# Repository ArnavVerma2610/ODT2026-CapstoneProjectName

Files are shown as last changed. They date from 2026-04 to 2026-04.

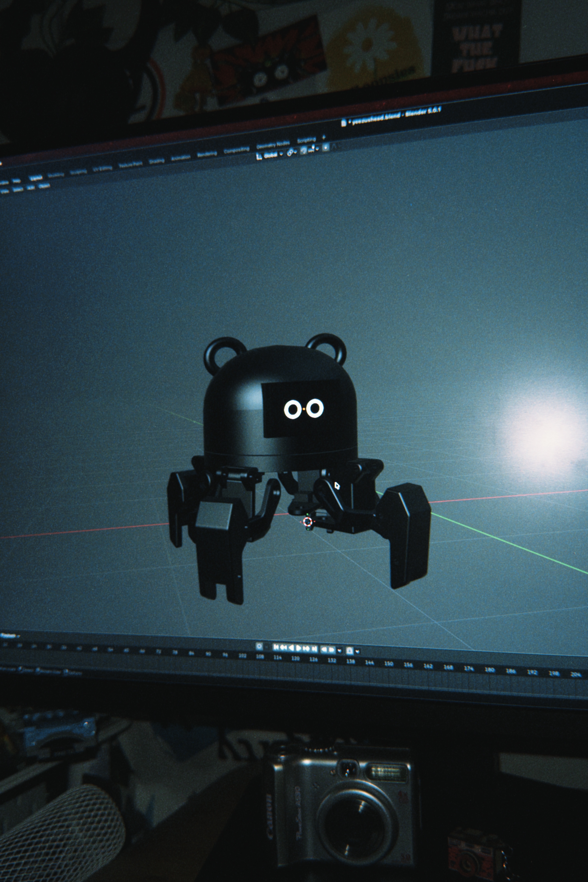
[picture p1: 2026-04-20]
Mechanical Details/Media/3D Visualization.JPG

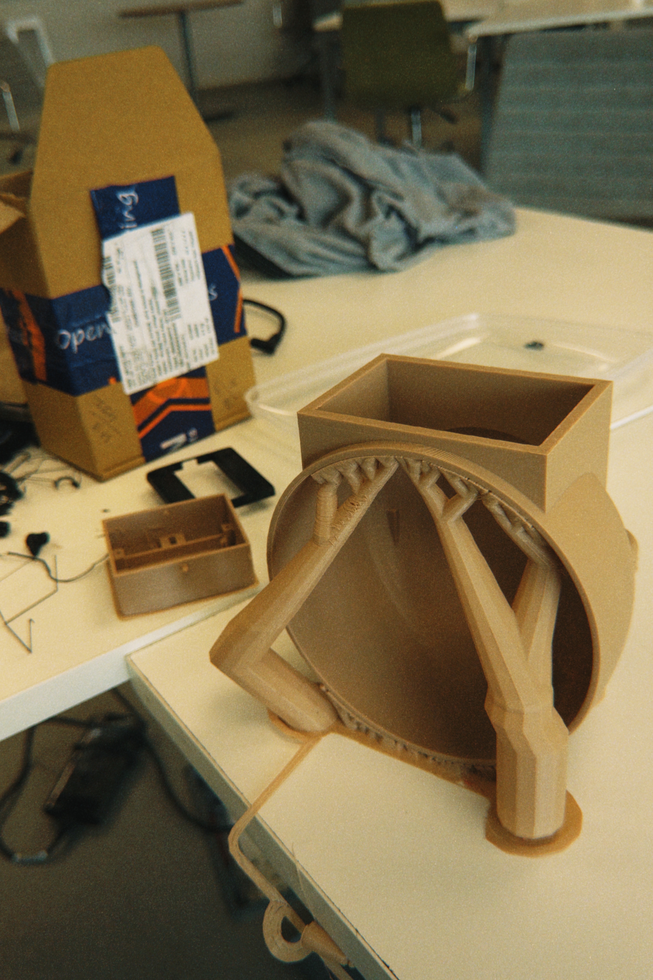
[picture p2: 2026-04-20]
Mechanical Details/Media/Head Print.JPG

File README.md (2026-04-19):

**Project Title**

Yeezus

**📌 Project Overview**

We are creating a small and friendly robot pet for entertainment purposes. It dances, greets, and even plays songs! Carrying with it a visualizer screen for both songs and character animations, it has 4 legs and can execute complex movements.

**📂 Repository Structure**
1. Electronics Details
2. Mechanical Details
3. Software Details
4. Project Documents
5. Media

**⚙️ How to Navigate This Repository**

Electronics Details → Circuit, components justification

Mechanical Details → Sketches, CAD, and fabrication

Software Details → Code, logic, and implementation

Project Documents → Design thinking, planning, testing

Media → Weekly progress and final output

**👥 Team Members**
Arnav Verma
Swayam Tayalia

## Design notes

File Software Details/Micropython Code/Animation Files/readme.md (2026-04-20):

Contains the original image sequence aswell as the .bin file flashed onto the ESP32

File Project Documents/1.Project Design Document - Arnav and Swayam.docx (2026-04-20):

# Project Design Document

### 1. Design Intent

- We set out to create a very fun and lighthearted experience with this project, create a fun project with ourselves to test our limits as people who had never touched electronics before this module began, to being a cute pet for people to look at and get attached to.
- It’s meant to act almost like a first prototype for a robotic pet for a kid, complete with animations and music aiming to stimulate.

### 2. Inspiration & References

- Inspired by Rocky from Project Hail Mary, R2D2 from Star Wars, The Graduation Bear by Kanye West

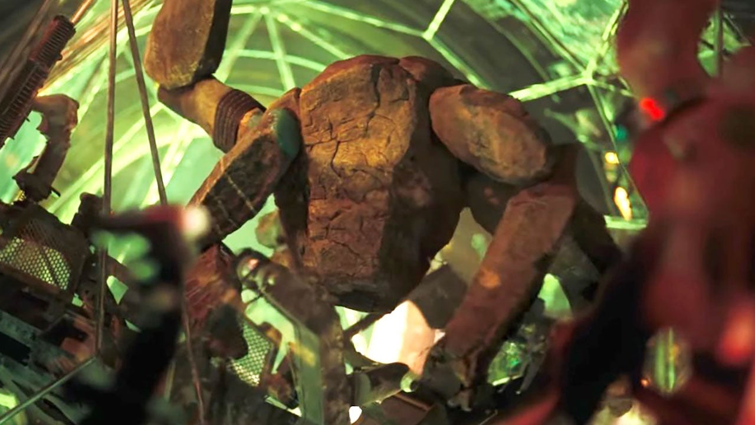
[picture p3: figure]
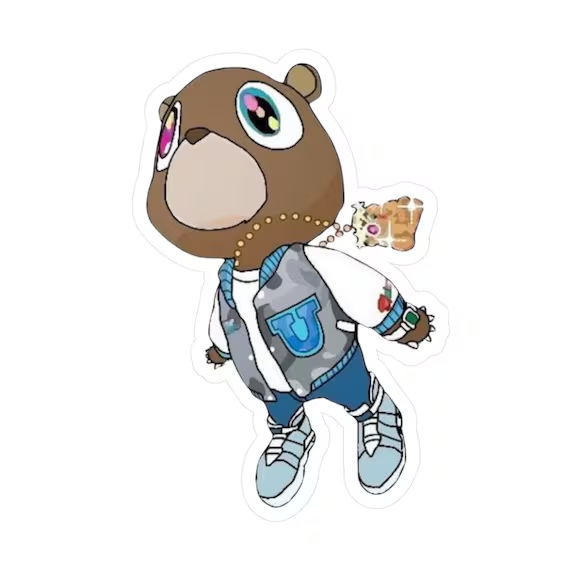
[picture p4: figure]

### 3. User Journey

Step-by-step experience of the user:

1. A user walks by this robot, standing on its stage, with a tablet beside it explaining what it is, what is does.
2. Intrigued, the user decides to flip the switch behind the bot’s head.
3. Suddenly, it comes to life, with a fun robotic voice and an animation making it seem friendly, it introduces itself, YeezyBot.
4. It goes through it’s routine, dances to a song, idles to a Mario Theme, and finally, it walks towards you, wanting to be your friend :)

### 4. Success Criteria

Define measurable success:

- Speaker and Animations startup in <1 second of each other
- User experience relies on the user only turning a switch on, and not having to interfere with any of the servo positions
- Animation goes through the entire 2:35 minute routine uninterrupted
- The robot doesn’t tip over or walk off its stage

### 5. System Overview

Yeezybot is an ESP32-based quadruped that performs a walking/dance routine with on-board OLED animation and audio playback. The ESP32 runs MicroPython and drives three peripheral subsystems . An I2C link (SCL=22, SDA=21, 400 kHz) talks to a PCA9685 16-channel PWM controller, which generates 50 Hz servo pulses for the eight leg servos — four hip joints and four knee joints arranged as a diagonal-trot gait with rear-biased back-lean to compensate for the front-heavy chassis. A dedicated SPI bus (SCK=18, MOSI=23, DC=2, RST=4, CS=5, 20 MHz) streams a 1,210-frame MONO_VLSB animation ( comp4.bin ) to a 128×64 SSD1309 OLED, with frame advances interleaved into the servo step loop so playback never stalls the walk. A DFPlayer Mini, driven over UART with its serial command protocol, plays the matching audio track from microSD in lockstep with the dance routine.

### 6. High-Level Block Diagram

👉 Visual diagram of system components and flow

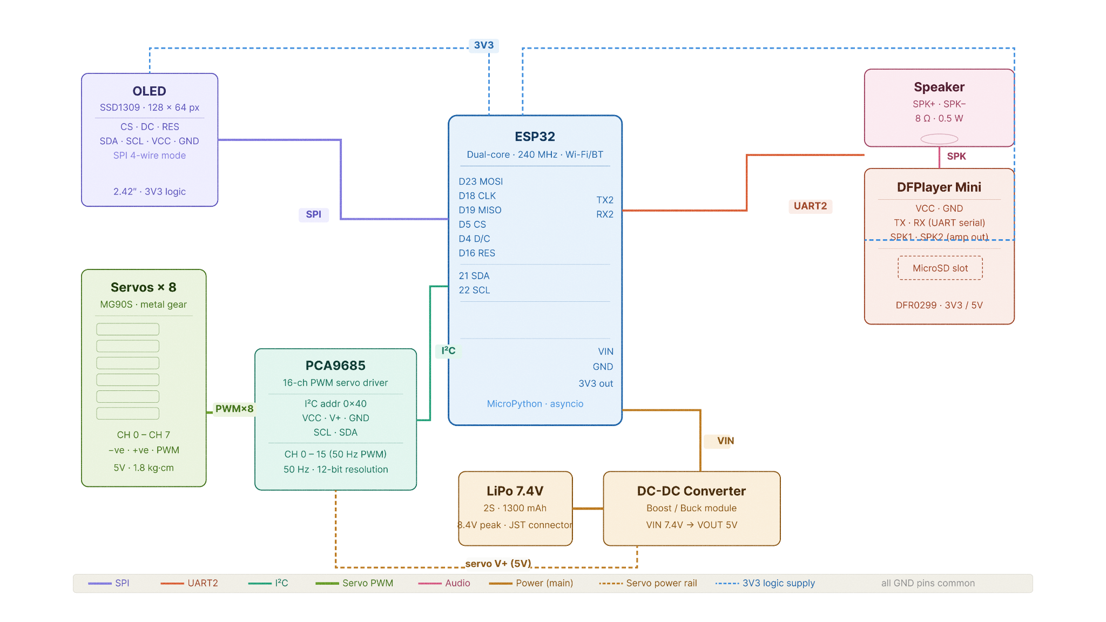
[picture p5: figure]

### 7. Input / Output Mapping

Input | Process | Output
7.4V power supply | Buck convertor | 5v power
Servo channels to pca9685 channels | Servo driver/i2c | Individual control over servos
esp32 | Pca9685 through SCL AND SDA | Control over channels on the driver
Micro SD Card | DF Player Mini | .mp3 files played over speaker
Imag sequences as bin files | SPI | OLED Display

### 8. Sketches & Concepts

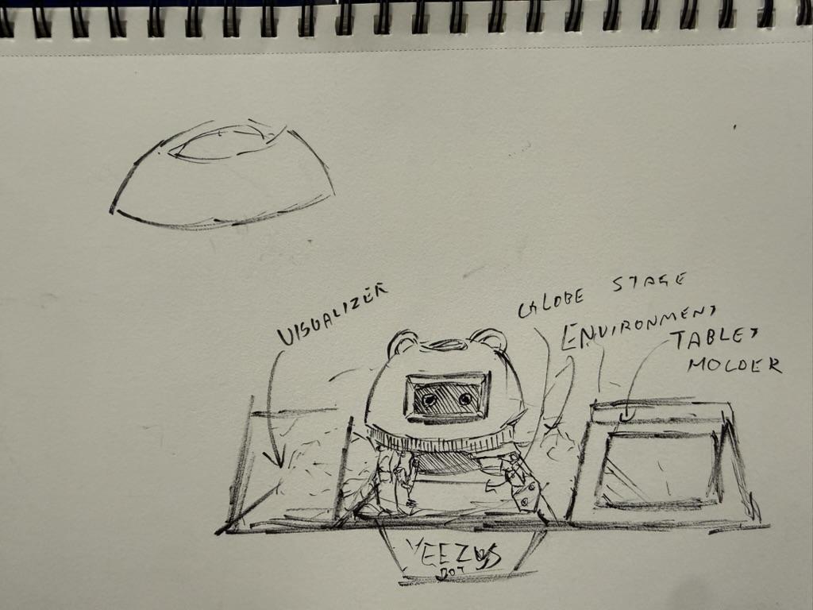
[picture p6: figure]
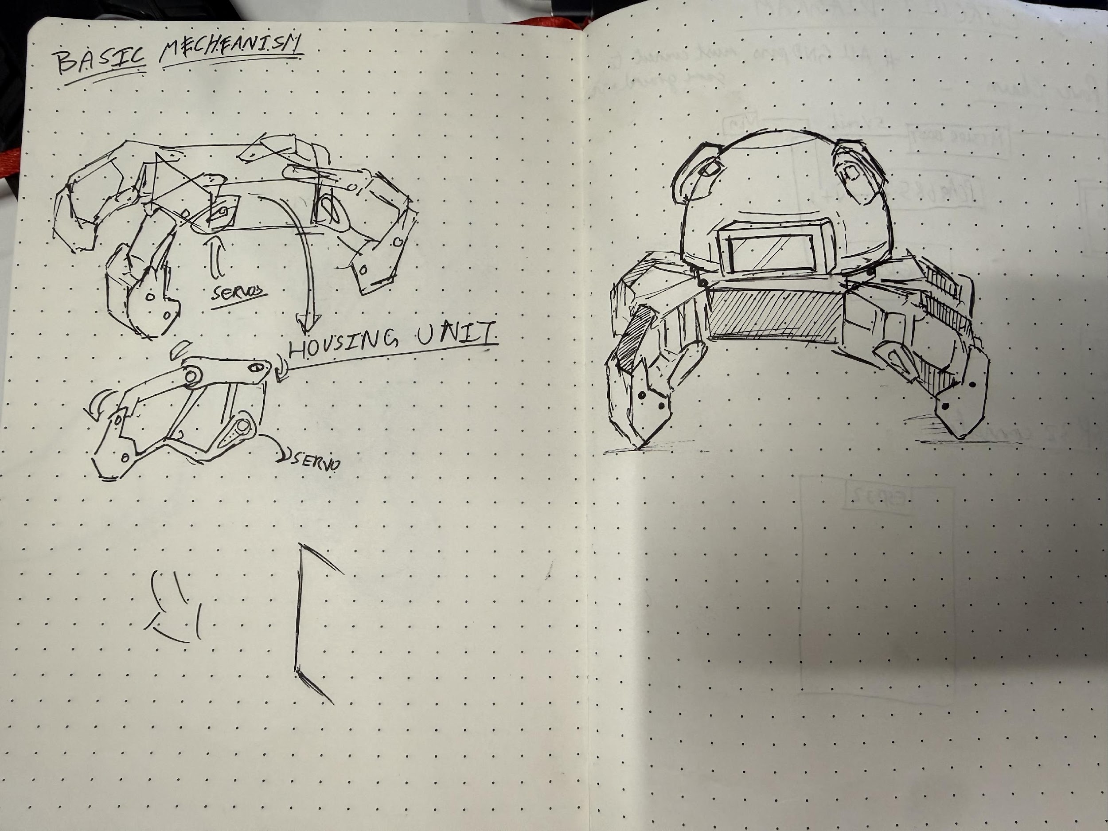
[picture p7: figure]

### 9. Final System Architecture (Labelled)

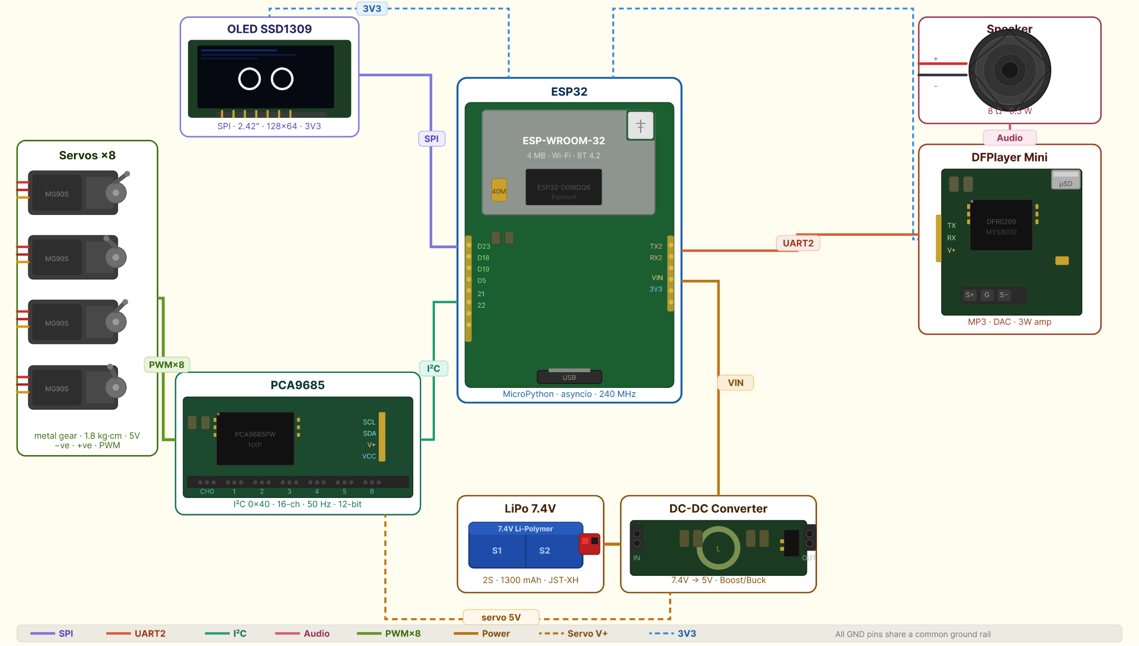
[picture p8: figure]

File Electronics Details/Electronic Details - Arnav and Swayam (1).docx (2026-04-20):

# Electronics Documentation

### 1. Electronics Block Diagram

INITIAL BLOCK DIAGRAM:

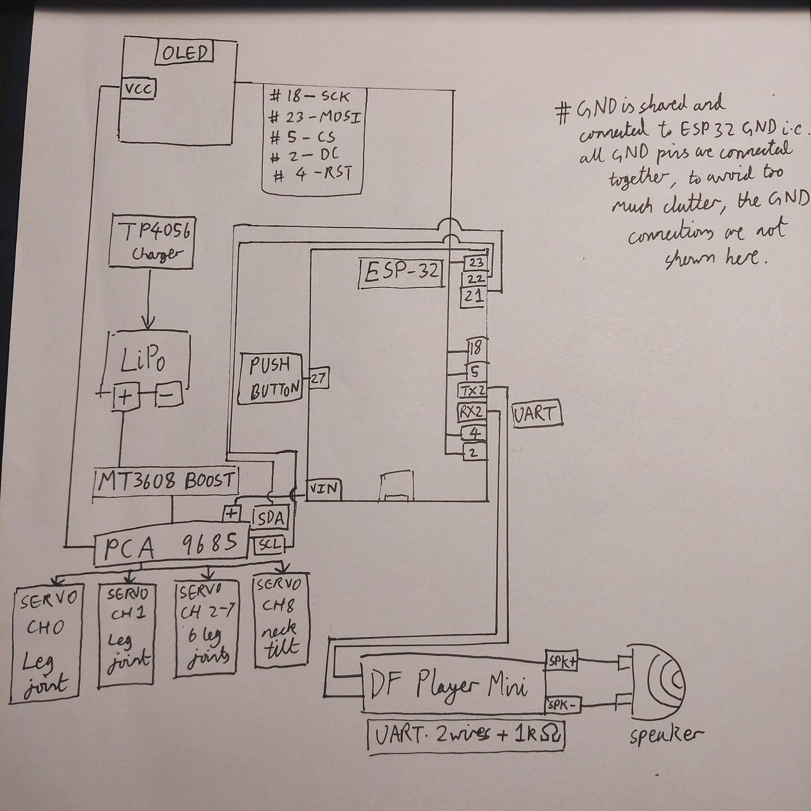
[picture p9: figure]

FINAL CIRCUIT/BLOCK DIAGRAM: (without updated switch connections)

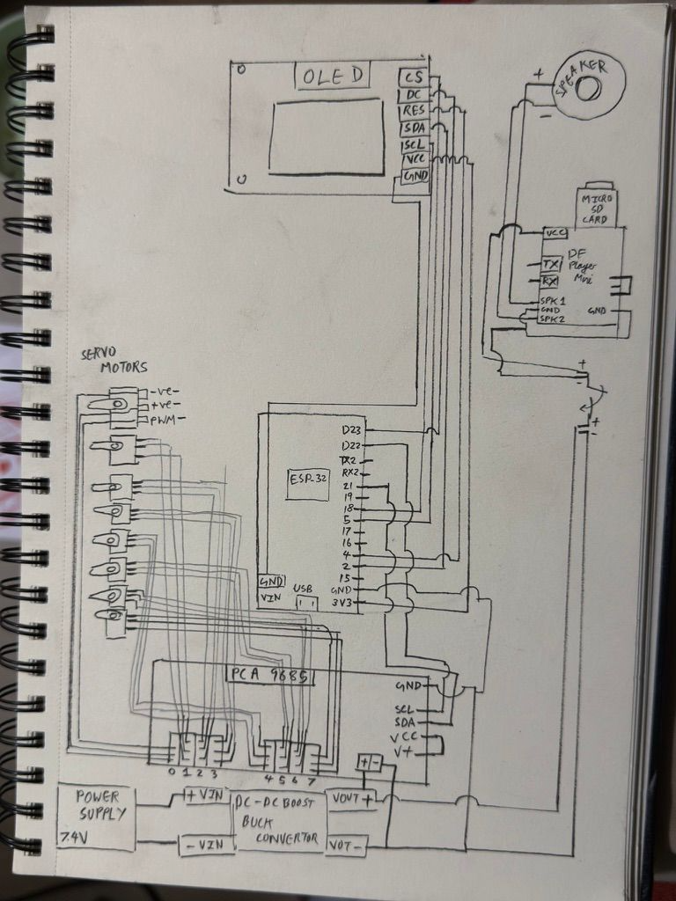
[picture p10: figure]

### 2. Components Table

Component | Quantity | Purpose | Justification
MG90 Servo motors | 8 | To move the individual hip and knee for all four legs in the quadropod | Servos provide robust and smooth motion and are small enough and multiple can be controlled at a time
PCA9685 | 1 | Provides PWM signals to control the position of multiple servo motors using i2c | We need a driver for all the servos and this is the most reliable one
DC-DC BOOST BUCK CONVERTOR | 1 | Converts incoming 7.4v to 5v | We need constant 5v power supply to the electronics in this circuit. We checked this using a multimeter
DF PLAYER MINI | 1 | Used to playback mp3 music from an sd card | Low cost mp3 module designed for audio playback and doesnt need to be connected to a microcontroller to just normally play audio tracks,avoids complexity
Speaker | 1 | Speaker is used to output the audio from the df player | We chose a 8 ohm, 0.5W cause of its small form factor and ease
ssd1309 oled display | 1 | Takes bit map images sent to it and converts it into sequences displayed on the screen | We chose this 2.4 inch display due to it’s high quality oled and larger pixel grid size

Justification is important

DETAILED OVERVIEW OF SERVO MOTORS AND CALIBRATION ‘

Each servo was connected to the channels of the pca9685 i.e. channels 1 to 7.

After this, each servo was placed into the 3d printed units, which would later prove to be a mistake as we had not calibrated it properly yet.

I originally tried to use the concept of oscillator, i.e. the sin wave concept inspired by how keyframe animations in the free software bottango.

We tried doing that in bottango:

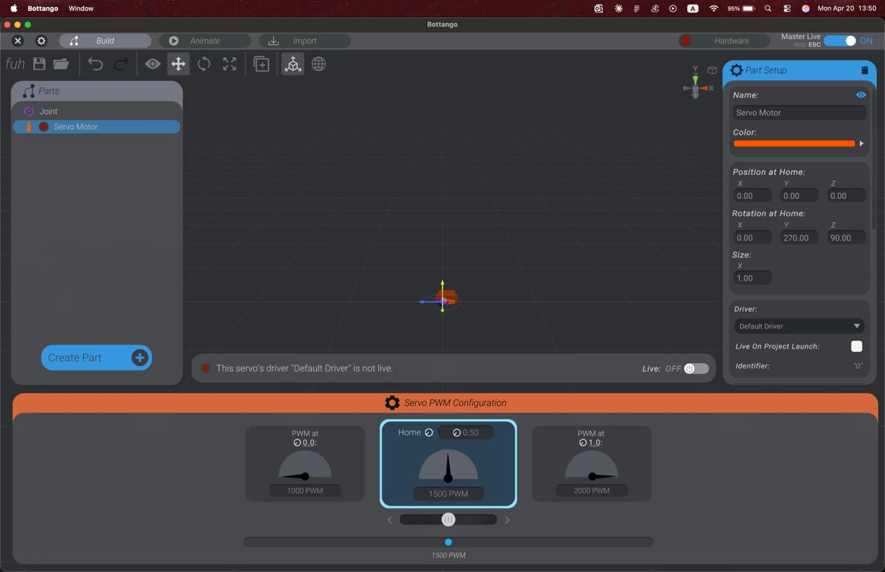
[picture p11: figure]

However, it failed as we were unable to convert the code into the numbers required for the servo animation and we struggled to understand what to extract from the C++ code.

We then decided we have to manually calibrate each servo

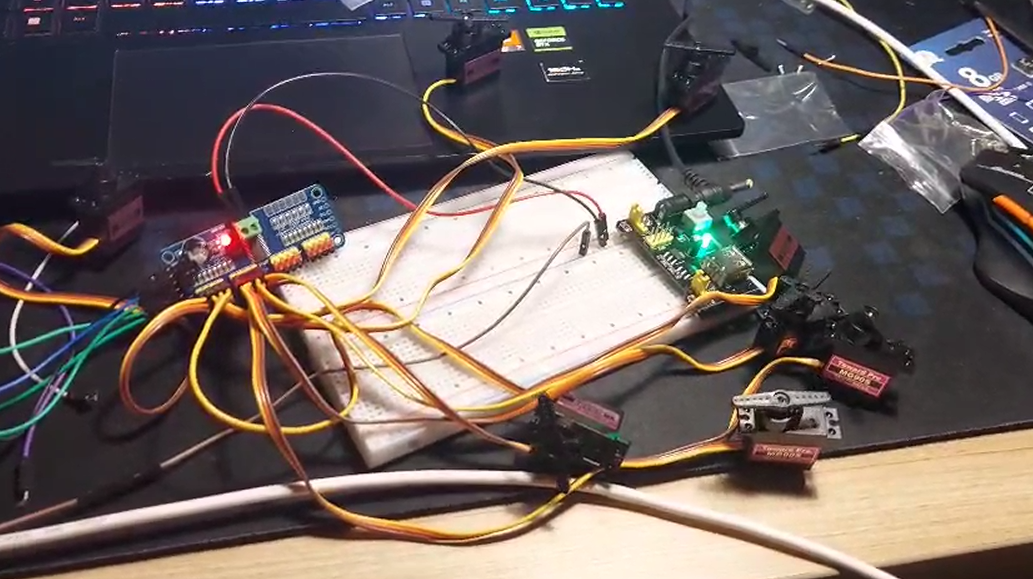
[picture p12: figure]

FOR THE CALIBRATION:

We ran an i2c based library for the pca9685. We then used it to run the respective servo movements for each channel and tested the direction of rotation and the angle swept, after heaps of trial and error not only with the direction of movement but making sure the shaft does not lock out of the housing of the hip and knee indentations cause calibration gets faulty once that happened.

We finally decided on the final calibration for each servo:

# Ch 0 = Front-Right TOP (hip) home=0 moves 0→90 (0=standing)

# Ch 1 = Front-Left TOP (hip) home=90 moves 90→0 (90=standing)

# Ch 2 = Back-Left TOP (hip) home=0 moves 0→90 (0=standing)

# Ch 3 = Back-Right TOP (hip) home=90 moves 90→0 (90=standing)

# Ch 4 = Front-Right BOTTOM (knee) home=0 moves 0→150 (0=standing)

# Ch 5 = Front-Left BOTTOM (knee) home=150 moves 150→0 (150=standing)

# Ch 6 = Back-Left BOTTOM (knee) home=0 moves 0→150 (0=standing)

# Ch 7 = Back-Right BOTTOM (knee) home=130 moves 130→0 (130=standing)

OLED LIBRARY AND CONNECTIONS WE USED FOR THE OLED:

BIN SEQUENCES FIRST DISPLAYED ON OLED USING TERMINAL

THE DF PLAYER MINI WAS WIRED DIRECTLY TO THE POWER SUPPLY AND SPEAKER AND MICRO SD CARD WAS USED TO STORE .MP3 FILES WHICH WERE PLAYED SEQUENTIALLY.

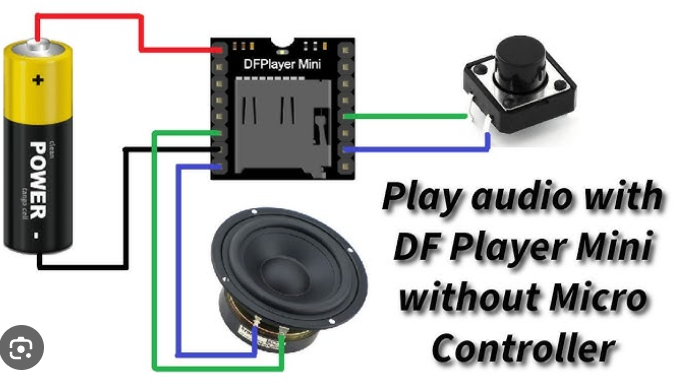
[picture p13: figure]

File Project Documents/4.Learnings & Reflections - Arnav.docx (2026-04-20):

# Learnings & Reflections Document

### 1. Team Reflection

The team worked to their strengths, each worked on different aspects of design, code, and hardware depending on what their strong suits were.

The ease of communication and work ethic helped ease workflow.

Team dynamics in terms of planning and overall execution of final result could be improved,

### 2. Technical Reflection

(add OLED and image bitmap related technical challenges here)

Key technical challenges:

DEBUGGING/PITFALLS FACED:

- MAKING THE INITIAL BLOCK DIAGRAM WAS TRICKY AND NOT THE MOST RELIABLE
- WOKWI SIMULATIONS FAILED TO WORK
- MODIFYING AND DESIGNING OUR PARTS IN FUSION TO FACILITATE SMOOTH MOVEMENTS TO FIT EACH MG90 WAS TEDIOUS
- BOTTANGO SIMS FAILURE
- SERVO CALIBRATION ISSUES
- OSSCILATOR ANIMATION SEQUENCE VERY UNRELIABLE, HARD-CODED ANGLE MOVEMENTS PREFERRED INSTEAD
- OLED INTERFACING, SPI CONNECTION FOR SSD1309 WAS MORE DIFFICULT THAN IF IT WAS I2C
- TRANSFERRING BITMAP IMAGE SEQUENCES TO THE OLED PROVED DIFFICULT IN MICROPYTHON COMPARED TO TERMINAL.
- GETTING THE OLED TO WORK ALONG WITH THE SERVOS INVOLVED

LEARNINGS:

SOFTWARE:

In terms of software, we learned a lot about how different protocols work, such as 12c, SPI, UART and how they depend on the data-driven and the supply of power they draw from. We also learned a lot about how to make sure to use external drivers to move servos, i.e., assigning channels to them, calling the functions to adjust the angles, and determining mean positions through trial and error.

We also learned about how OLEDs work and how they convert images into bitmaps, and how SPI connections work, along with the correct prompt engineering to correctly convert the image sequences and display them through the terminal and later Python.

We learnt how to use oscillator math functions such as sin(2pi + phase offset) , which didn't end up working, but also made us more confident in hard function calling and angle resent animation based solely on the list of angles between max and min after calibration.

We got through code flashing and created an MIT App Inventor base app to run different animated commands, such as walk, dance

HARDWARE:

Getting all the parts 3d printed and then getting all the parts sanded, taking off supports was harder than expected cause we had to also model a lot of the mg90 attachment parts inside of fusion while taking reference from repos online such as https://github.com/dorianborian/sesame-robot/

Figuring out the m3 scews and hard clamp fits while not already calibrating the servos was very difficult and then having to calculate the angles which trying and failing at an oscillation sine curve type movement was a waste of time

End of the day calibrating and setting max and min values to each servo and carefully placing them in the housing was the main part

On the final day , assembling all the parts was causing weight issues as the physics of the weight of all components and the battery proved to heavily hamper the final output

### 3. Design Reflection

From a design point of view our end result matched the initial ideation stages pretty well, the look of the robot was pretty similar to out initial sketches.

The experience far surpassed our intentions.

- The experience of it definitely matched the intent we originally we went out with. We thought this would be a much simpler robot, maybe move left or right a little, but not really do much, definitely not a fully choreographed dance sequence and be able to walk around, but that’s the fun part of ambition, that even after all of that, we’re still left with a semi-satisfied feeling. That’s important though, that’s the only feeling that will really drive us forward and push us to improve for the next time we dabble in this field.

### 4. Personal Reflection

What did I end up learning throughout this module? Everything. Despite my preconceived notions of not having loved Computer Science too much during my high school years, I ended up loving the process of interfacing physical electronics with code in this module and realized that perhaps that tactility was the missing link in me developing a love for this field. I truly enjoyed my time throughout the module and only wished we’d gone through this sooner. I really struggled with the hardware part since code was just a more familiar and comfortable medium for me but slowly throughout the module I understood what worked and it all started clicking for me. I even started a few side projects of my own and dug deeper into this rabbit hole, even though it’s actively burning a hole in my pocket. Thank you to Nayan for really guiding me throughout this, couldn’t have made it through without you.

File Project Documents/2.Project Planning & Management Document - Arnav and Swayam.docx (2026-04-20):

# Project Planning & Management Document

### 1. Project Overview

- Name: YeezyBot
- Team: Arnav Verma and Swayam Tayalia
- Overview: We are creating a small and friendly robot pet for entertainment purposes. It dances, greets, and even plays songs! Carrying with it a visualizer screen for both songs and character animations, it has 4 legs and can execute complex movements.

### 2. Team Roles & Responsibilities

Member Name | Role | Responsibilities
Arnav Verma | Software and Creative Elements | OLED Animation, Servo Animation, 3D Modeling, Media, Documentation, Video Editing, Diorama Creation, MIT App, and HTML File
Swayam Tayalia | Hardware Wiring and Software Testing | Housing unit and legs assembly, Servo Wiring, Servo Calibration and Troubleshooting, Speaker Electronics, 3D Modeling, Diorama Creation, Documentation

👉 Clearly define who is responsible for what (software, electronics, documentation, etc.)

### 3. Project Timeline & Milestones

Week | Goals | Deliverables | Status
Week 0 | Iterate over what the design should be , its functionality, feasibility and basic circuitry | Project design , idea and function | complete
Week 1 | Get 3d files ready and component list,block diagram | 3d print files, components order | complete
Week 2 | 3d parts ready to assemble and | 3d printed parts , components connected and tested | complete
Week 3 | Final project ready with at least 2 animation cycles | Final hardware assembly and complete software integration | Tentative - janky setup

👉 Break project into weekly achievable goals

### 4. Weekly Progress Log

A table for each week:

Week 0

- Planned Tasks: think and iterate over a project idea
- Completed Tasks: finalised an idea
- Challenges Faced: going from extremely complex idea to a slightly less complex one
- Solutions: focus on step by step process and not go in head first
- Next Steps: gather parts, circuit diagram , plan out the next weeks

Week 1

- Planned Tasks: get a complete circuit diagram, order the parts, get reference from other github repositories online as well as quadropod videos on youtube.

Get the 3d print files ready, edit and modify existing files as well as put new files

- Completed Tasks: got a complete block diagram and ordered parts
- Challenges Faced: tried and failed simulating in wokwi
- Solutions: ask nayan
- Next Steps: refine the idea, wait for parts and start assembling,testing

Week 2

- Planned Tasks: test and start putting components and circuits together, get parts 3d printed
- Completed Tasks: tested components, failed to simulate in wokwi completely, few failed prints , but rest of the prints worked.
- Challenges Faced: having to change the circuit diagram and having to refer to many repos online and yt vids to figure the correct connections
- Solutions: do more research and work fast
- Next Steps: do final circuit, test out animations, prepare final code and assembly

Week 3

- Planned Tasks: do final circuit, test out animations, prepare final code and assembly
- Completed Tasks: final circuit, animations - janky , final code
- Challenges Faced: weight distribution , connection issues, hefty components to fit inside small space., janky animations
- Solutions: improve connections, modify entire project to counteract the weight of the battery and other components
- Next Steps: work on new animation cycles, better walk and dance and do more research to see how project can be modified to balance weight better.

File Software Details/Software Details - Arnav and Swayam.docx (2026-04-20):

# Software Documentation

### 1. Software Overview

SOFTWARE COMPONENTS:

OLED BITMAP IMAGE SEQUENCES

SERVO MOTOR LISTS AND FUNCTIONS FOR THEIR MOVEMENT

DIFFERENT CYCLES FOR THE SERVO MOTOR including WALK and DANCE Cycles.

PLATFORMS USED:

Micropython, Bottango, Terminal (for the test of the OLED Display)

The software handles the primary code, importing libraries from machine including i2c,spi and uart protocol logic.

The primary code contains the oled library import with the bin images and the servo controls.

### 2. System Logic

1.User turns on the switch or plugs in the micro-USB

2. The power supplies 7.4V to a buck converter

3. The DC-DC boost buck convertor steps down the voltage to 5V

4. The signal goes to the DF Player mini to access the files from the micro-SD card that end with .mp3 and plates them sequentially through the connected speaker.

5. The OLED Starts displaying the bitmap image sequences from a preset animation that was created and then converted to this format to be displayed on to the screen

6. The HOME POSITION of the servos gets triggered i.e. the mean position of the servos.

7. The Burst animation is triggered

8. DANCE - animation cycle is triggered - twist, lean , tilt , wave etc.

9. The USB is connected and a walking cycle animation can be played using walk cycle code on laptop that can be adjusted per cycle.

10. Animation ends, music stops , returns back to HOME position.

3.FLOWCHART:

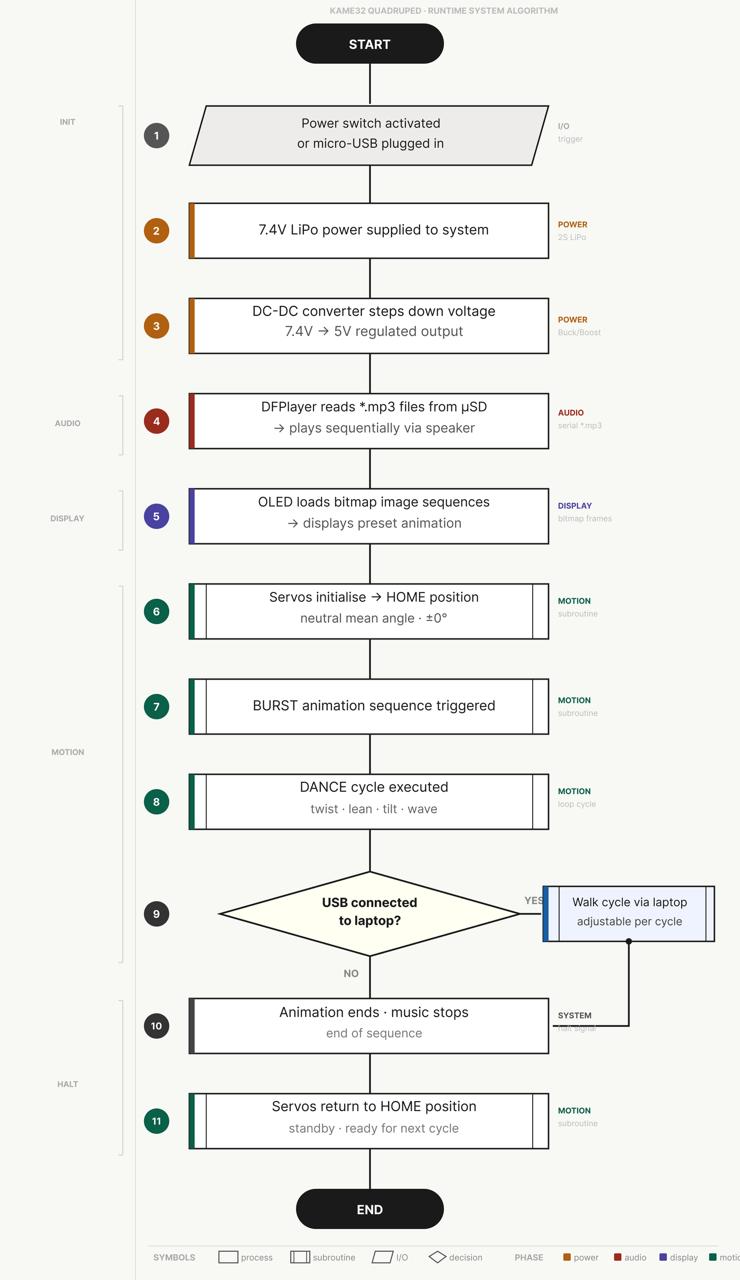
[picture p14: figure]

### 4. App Flow (If MIT App Inventor)

Base MIT App Inventor (Used as a stepping stone to the HTML Website)

- Start Scanning → scans for BLE devices, populates list live
- ListView tap → selects device
- Connect → connects to selected device
- Disconnect → disconnects
- CobraKai / Bob / Wave / Dance → all four send identical byte [1] to the ESP32 (bug — never differentiated, meant to be fixed in html file)
- Clock timer polls for incoming strings, displays them in status label

HTML File

- Start Scanning → opens browser's native BLE picker
- Device tap → selects device
- Connect / Disconnect → same behavior
- CobraKai / Dance / Wave / Bob → each sends a function call

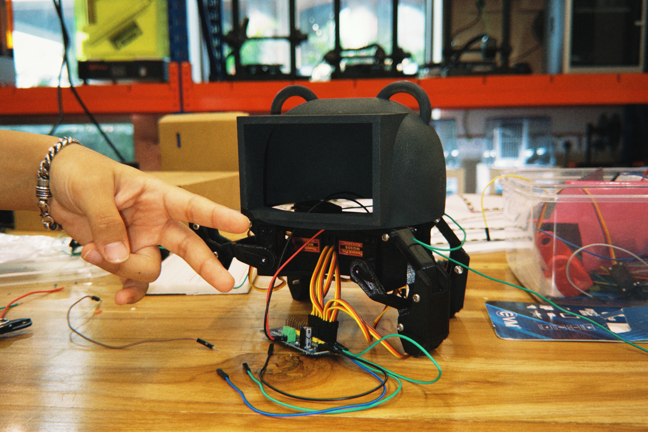
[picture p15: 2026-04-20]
Mechanical Details/Media/Head ontop of Body Frame.JPG

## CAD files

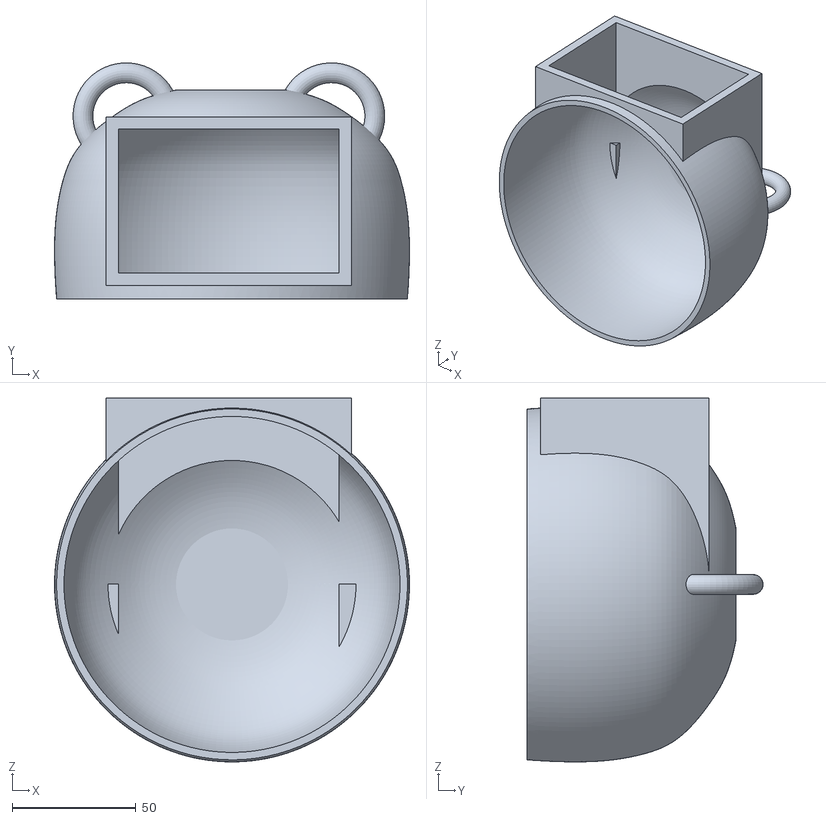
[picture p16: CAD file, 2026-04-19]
Mechanical Details/Fabrication Files /DROID HEAD .stl
143.3 x 95.3 x 146.8

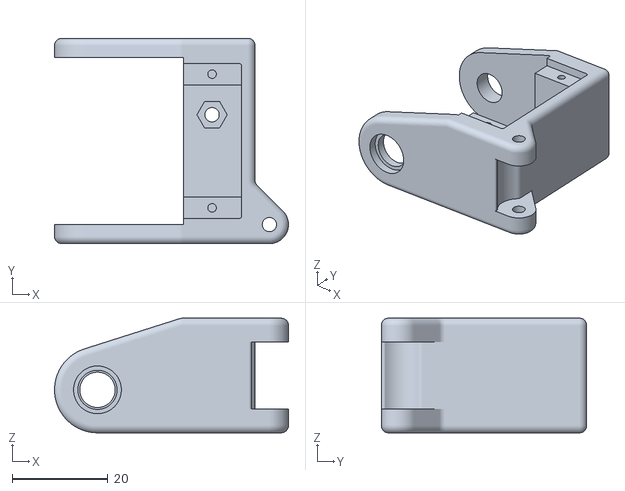
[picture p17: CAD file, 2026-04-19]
Mechanical Details/Fabrication Files /bracket-right-mg90s.stl
49.0 x 43.0 x 24.0

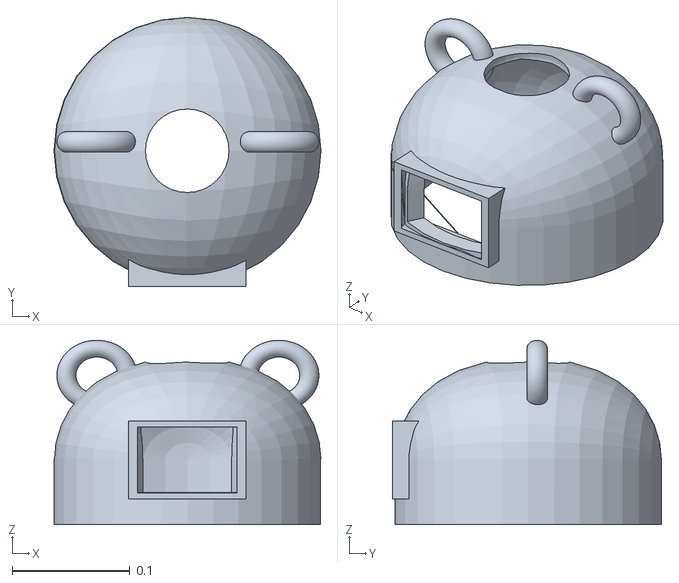
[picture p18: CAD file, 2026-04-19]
Mechanical Details/Fabrication Files /headzozo.stl
0.227 x 0.229 x 0.157

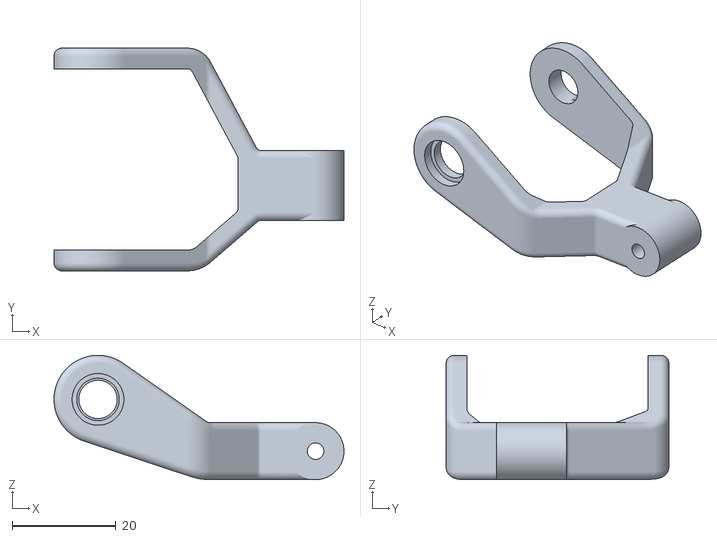
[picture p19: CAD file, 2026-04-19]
Mechanical Details/Fabrication Files /leg-right-mg90s.stl
56.0 x 43.0 x 24.0

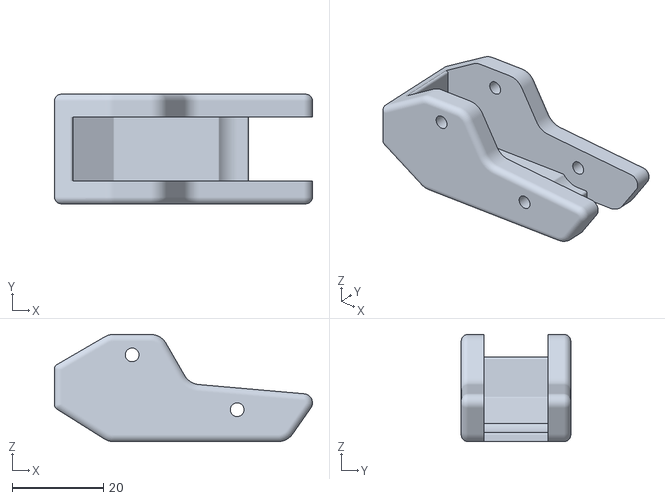
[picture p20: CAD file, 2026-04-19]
Mechanical Details/Fabrication Files /foot.stl
56.5 x 24.0 x 23.5

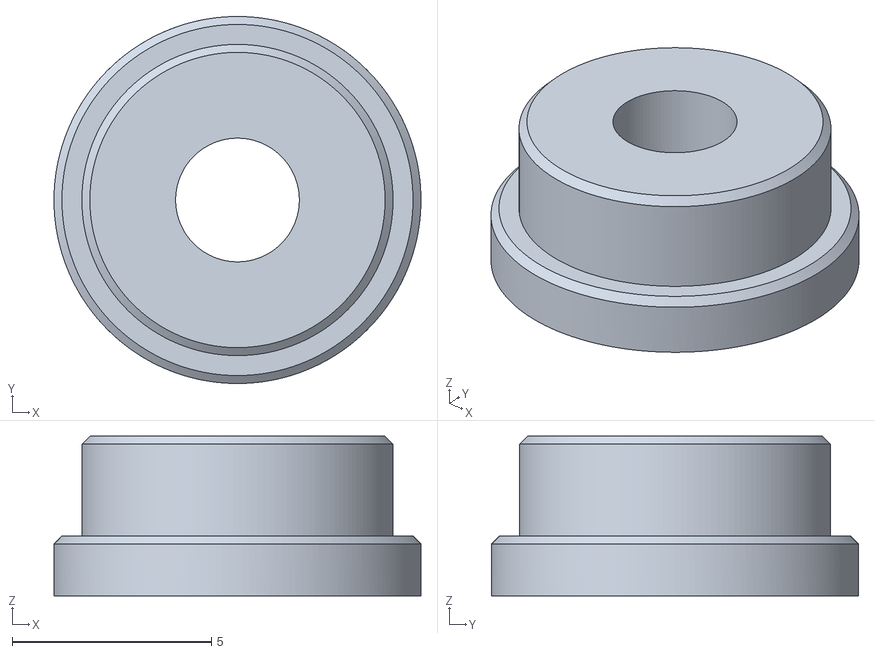
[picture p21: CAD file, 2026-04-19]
Mechanical Details/Fabrication Files /bushing.stl
9.20 x 9.20 x 4.00

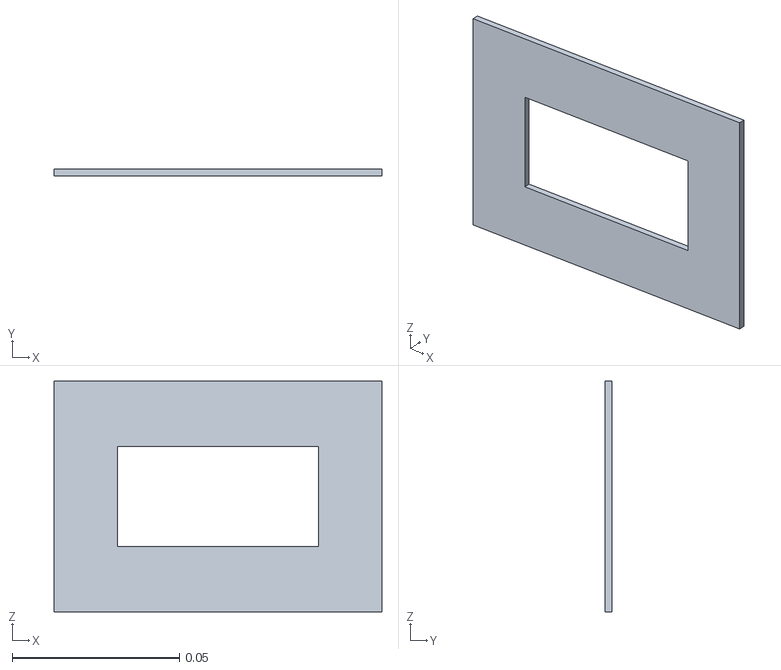
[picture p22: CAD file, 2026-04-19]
Mechanical Details/Fabrication Files /faceplate.stl
0.098 x 0.002 x 0.069

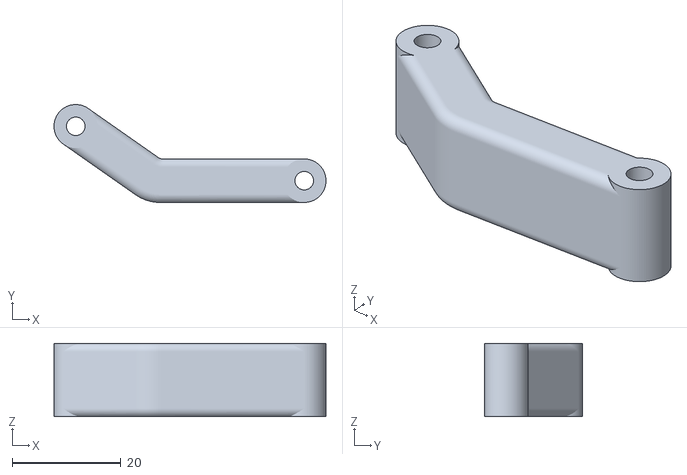
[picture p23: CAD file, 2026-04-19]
Mechanical Details/Fabrication Files /leg-link.stl
50.0 x 18.0 x 13.5

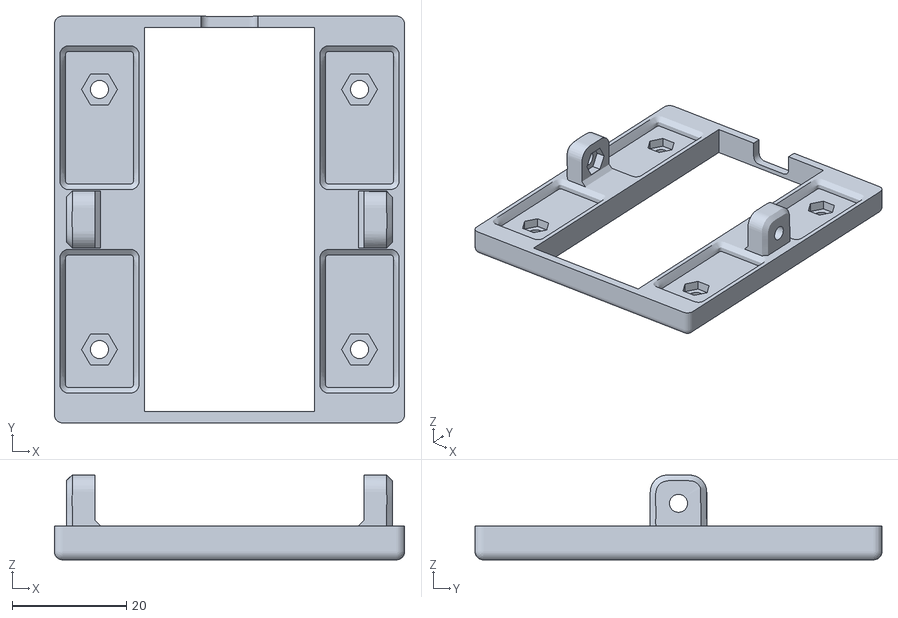
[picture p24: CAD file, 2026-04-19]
Mechanical Details/Fabrication Files /body-cover updated .stl
61.3 x 71.2 x 14.8

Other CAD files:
Mechanical Details/Fabrication Files /leg-left-mg90s.stl
Mechanical Details/Fabrication Files /faceplate.blend
Mechanical Details/Fabrication Files /yeezushead.blend

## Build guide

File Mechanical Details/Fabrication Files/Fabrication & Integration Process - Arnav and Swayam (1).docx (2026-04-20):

# Fabrication and Integration Process

### 1. Material Choice Justification :

Chose PLA for 3D printing for access to multiple colours and easier to manipulate post-print. Much lighter weight than resin, making it easier on the motors.

Chose MDF for the face plate to be able to easily laser cut and get precise dimensions quickly leaving room for iterations.

The parts were snap fit attached according to the movement of the mg90 servos and held together using m3 screws. The parts were sanded and snug but fluid movement was tweaked and refined.

Chose Extruded Polystyrene (XPS) Foam / High-Density Polyurethane (PU/PUR) Foam for the environment mainly for its shapeability and durability, along with its ability to hold the spray paint colours well.

2. Fabrication Steps :

1: 3D-Printing test parts for the servo motor housing

2: 3D-Printing the final servo motor housing

3: 3D-Printing the head of the bot

4: Laser-Cutting the face plate

5: Cut up XPS/PU/PUR Foam pieces into rocks and a globe stage for the environment and tablet stand.

DETAILED OVERVIEW OF THE HOUSING UNIT ASSEMBLY:

ISSUES FACED WHILE DOING THIS:

1. STRUGGLE TO FIND THE EXACT SCREWS WE NEEDED
2. THE PARTS WERE A VERY SNUG FIT, NO ROOM FOR SLACK
3. THE SUPPORTS REQUIRED SANDING AND AFFECTED QUALITY OF PRINTS

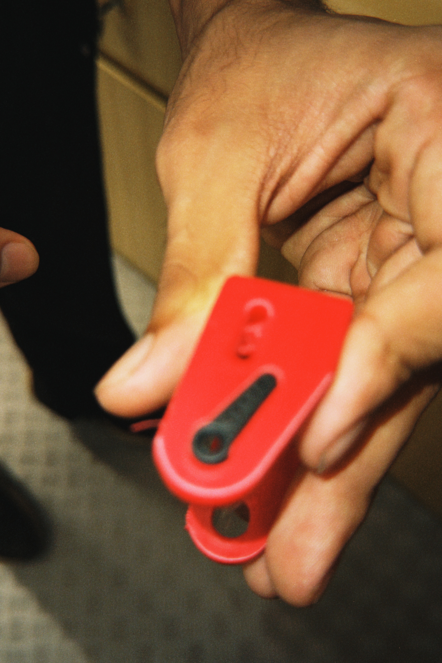
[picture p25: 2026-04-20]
Mechanical Details/Media/Test Print.JPG

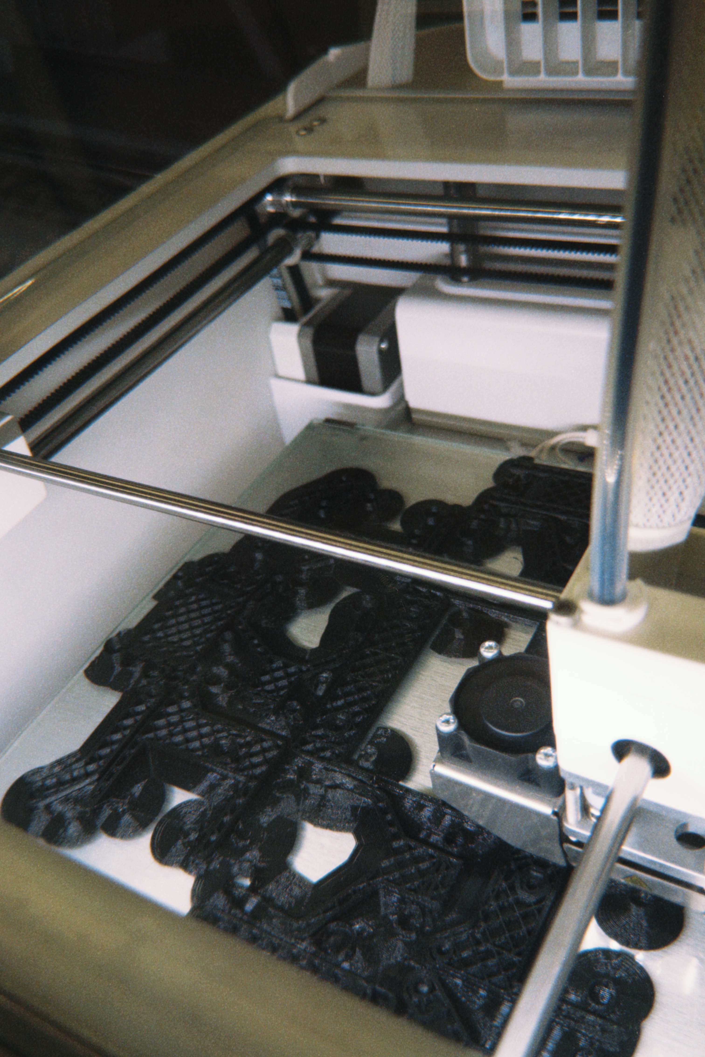
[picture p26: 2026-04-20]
Mechanical Details/Media/3D Printing final servo motor housing.JPG

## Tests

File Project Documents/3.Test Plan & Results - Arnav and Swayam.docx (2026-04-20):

# Test Plan & Results

### 1. Test Plan

Test | Method | Expected Result
We tested out if another person could hear the speaker and recognise that the dance would be synced | Outside person as a control setup to see if the message was conveyed | Success , with very janky movements

### 2. User Testing

- Fellow batchmates
- Asked to look at fluidity of leg movements and see if the dance synced to the music.

### 3. Results

Test | Outcome | Pass/Fail
1 | Almost all were at least amused | Pass

### 4. Observations

- Thought it was cute and entertaining , however we wanted them to be more amazed by it , but was unable to due to jank.
- Hard to user test a project like this

### 6. Improvements Suggested

- Fix the janky movements , get the servos to know the corresponding movements

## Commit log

2026-04-19 3d files and project files added
    [DROID HEAD .stl, body-cover updated .stl, bracket-right-mg90s.stl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]
2026-04-20 shifted files
    [DROID HEAD .stl, body-cover updated .stl, bracket-right-mg90s.stl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]
2026-04-20 Rename image_2026-04-20_154912169.png to Stage Diorama Sketch
2026-04-20 Rename image_2026-04-20_162545339.png to Circuit Diagram
